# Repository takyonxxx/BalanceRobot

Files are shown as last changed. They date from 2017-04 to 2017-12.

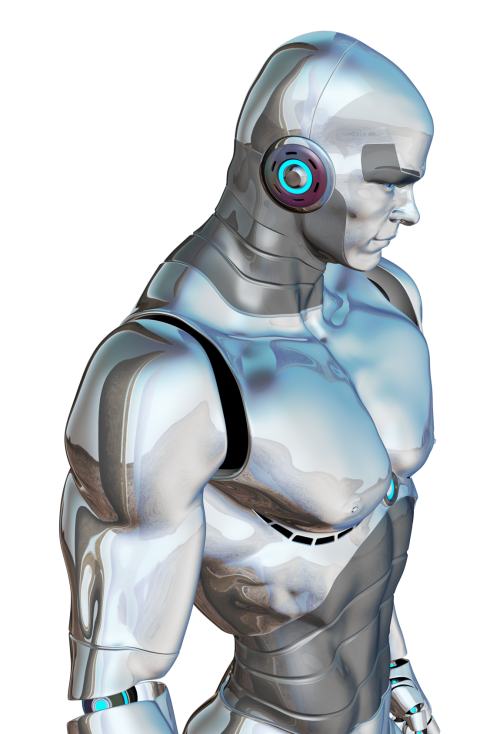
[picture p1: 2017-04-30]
Android/BalanceRobot/PNGPIX-COM-Robot-PNG-Transparent-Image-500x734.png

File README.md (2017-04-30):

Balance Robot Arduino Due or Mega

The Balance Robot uses:

18650 battery holder,

Arduino DUE / MEGA,

2 x 12V 37mm 350 Rpm 30:1 DC GearMotor with Encoder

MPU6050 (6-axis motion-tracking device that combines a 3-axis gyroscope and a 3-axis accelerometer)
With MPU6050 , you can get stable angle when the Kalman filter is used.

L298P motor driver:
is a high voltage (50V), high current (2A) dual channel full-bridge driver.
It can drive inductive loads such as relay, DC, and stepping motors.

Serial Bluetooth Module HC-06

Acrylic board

Video:
https://vimeo.com/212365258

Calibrating your PID Controller

Create some way in which you can change the PID constant of your robot while it is running.
One option is to use a potentiometer or some other analogue input to be able to increase or decrease the PID constant. 
I personally used the USB connection and the serial monitor to send new PID values.
This is important as you can then see straightaway how well the new PID values are working, and you won’t have to re-upload the code hundreds of times!
Set all PID constants to zero. This is as good a place to start as any…
Slowly increase the P-constant value.
While you are doing this, hold the robot to make sure it doesn’t fall over and smash into a million pieces!
You should increase the P-constant until the robot responds quickly to any tilting, and then just makes the robot overshoot in the other direction.
Now increase the I-constant.
This component is a bit tricky to get right.
You should keep this relatively low, as it can accumulate errors very quickly.
In theory, the robot should be able to stabilise with only the P and I constants set, but will oscillate a lot and ultimately fall over.
Raise the D-constant.
A lot. The derivative components works against any motion, so it helps to dampen any oscillations and reduce overshooting.

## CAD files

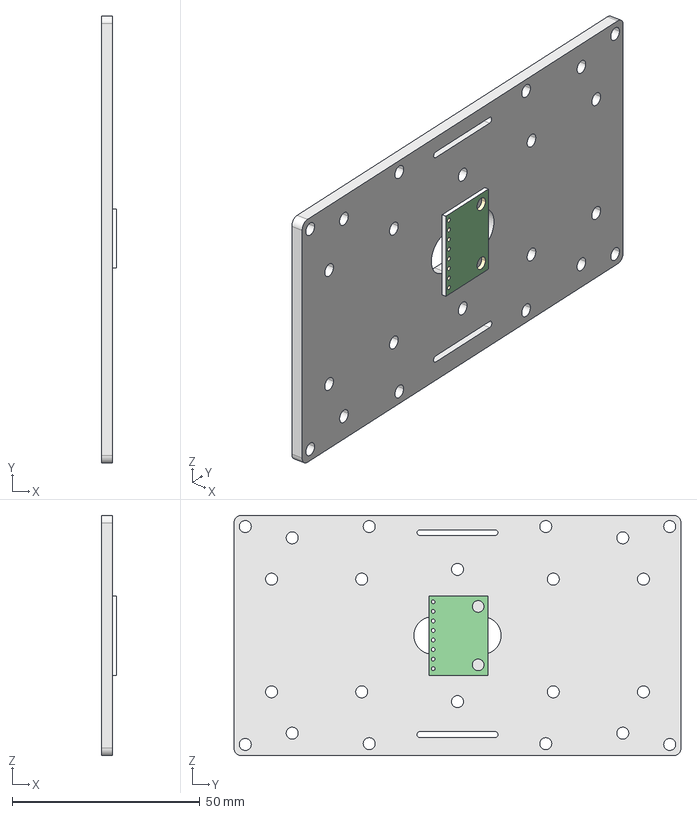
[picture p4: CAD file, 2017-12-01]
balance_mpu6050.stp
4.08 x 119.0 x 64.0 mm

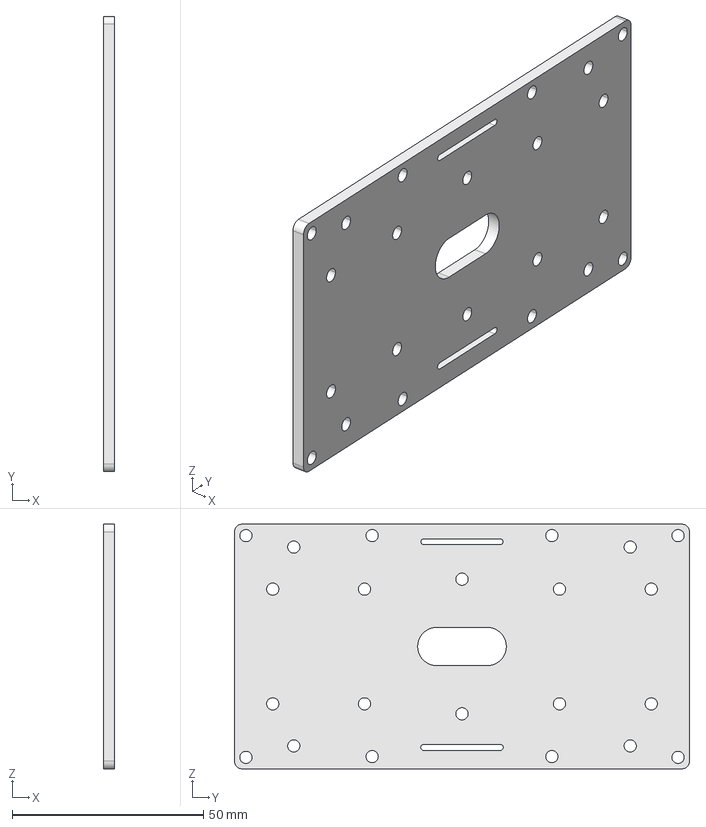
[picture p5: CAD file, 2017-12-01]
balancerobot.stp
3.00 x 119.0 x 64.0 mm

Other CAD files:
balancerobot2d.fcstd
balancerobot.stl

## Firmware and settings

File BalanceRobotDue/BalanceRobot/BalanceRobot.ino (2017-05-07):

#include <Wire.h>
#include <Kalman.h> 
#include "ComPacket.h"
#include <DueFlashStorage.h>
#include "NewPing.h"
#include "PID_v1.h"

#define RESTRICT_PITCH 
#define GUARD_GAIN 5

//motor  define L298P
#define PWM_L 2  //M1 ENA
#define PWM_R 3  //M2 ENB

#define pingPin 9 // Trigger Pin of Ultrasonic Sensor
#define echoPin 8 // Echo Pin of Ultrasonic Sensor

#define DIR_L1 5 //IN2
#define DIR_L2 4 //IN1
#define DIR_R1 7 //IN4
#define DIR_R2 6 //IN3

//encoder define
#define SPD_INT_R 13   //interrupt R
#define SPD_PUL_R 12  
#define SPD_INT_L 11   //interrupt L
#define SPD_PUL_L 10   

// Rutine for repeat part of the code every X miliseconds
#define runEvery(t) for (static long _lasttime;\
                         (uint16_t)((uint16_t)millis() - _lasttime) >= (t);\
                         _lasttime += (t))

#define MAX_DISTANCE 200 // Maximum distance we want to ping for (in centimeters). Maximum sensor distance is rated at 400-500cm.
NewPing sonar(pingPin, echoPin, MAX_DISTANCE); // NewPing setup of pins and maximum distance.

// kalman variables for sonar
float varSonar = 1.12184278324081E-05;  // variance determined using excel and reading samples of raw sensor data
float varProcess = 1e-8;
float Pc = 0.0;
float G = 0.0;
float P = 1.0;
float Xp = 0.0;
float Zp = 0.0;
float Xe = 0.0;

float distance = MAX_DISTANCE;

Kalman kalmanX; 
Kalman kalmanY;

ComPacket SerialPacket;

/* IMU Data */
double accX, accY, accZ;
double gyroX, gyroY, gyroZ;
double temperature;
int16_t tempRaw;

double gyroXangle, gyroYangle; // Angle calculate using the gyro only
double compAngleX, compAngleY; // Calculated angle using a complementary filter
double kalAngleX, kalAngleY; // Calculated angle using a Kalman filter

uint32_t timer;
uint8_t i2cData[14]; // Buffer for I2C data


int Speed_L,Speed_R;
int mSpeed,pwm_l,pwm_r;

int Speed_Need,Turn_Need;
int Speed_Diff,Speed_Diff_ALL;

double Angle_Car;
double Gyro_Car;
double Correction;

char buf[100];

uint8_t sensorPin = A0; 


//speed control values
long lastSpeedError = 0;
long speedAdjust = 0;
long dSpeedError,adjustLMotor,adjustRMotor;
long SKp ,SKi ,SKd;

int Position_AVG = 0;

float ftmp = 0;

DueFlashStorage dueFlashStorage;

struct storedData {
  float kp;
  float ki;
  float kd;
  int kc;
};

storedData m_storedData;

/////////////

#define SAMPLE_TIME 10

double Setpoint, Input, Output;

double aggKp, aggKi, aggKd;

//Specify the links and initial tuning parameters
PID balancePID(&Input, &Output, &Setpoint, aggKp, aggKi, aggKd, DIRECT);

void setup() {

  Serial.begin(115200);
  Serial1.begin(115200);

  aggKp=190;
  aggKi=425;
  aggKd=2.55;
   
  Serial.print("\nBalance Robot Initializing...\n"); 

  uint8_t codeRunningForTheFirstTime = dueFlashStorage.read(0); // flash bytes will be 255 at first run
 
  if (codeRunningForTheFirstTime) {    
    /* OK first time running, set defaults */
    m_storedData.kp = aggKp;
    m_storedData.ki = aggKi;
    m_storedData.kd = aggKd; 
    m_storedData.kc = Correction; 
    
    // write configuration struct to flash at adress 4
    byte b2[sizeof(storedData)]; // create byte array to store the struct
    memcpy(b2, &m_storedData, sizeof(storedData)); // copy the struct to the byte array
    dueFlashStorage.write(4, b2, sizeof(storedData)); // write byte array to flash

    // write 0 to address 0 to indicate that it is not the first time running anymore
    dueFlashStorage.write(0, 0); 
  }  
 
 /* read configuration struct from flash */
  byte* b = dueFlashStorage.readAddress(4); // byte array which is read from flash at adress 4
  storedData configurationFromFlash; // create a temporary struct
  memcpy(&configurationFromFlash, b, sizeof(storedData)); // copy byte array to temporary struct

  aggKp = configurationFromFlash.kp;
  aggKi = configurationFromFlash.ki;
  aggKd = configurationFromFlash.kd;
  Correction = configurationFromFlash.kc;

  Serial.print("Kp:");
  Serial.print(aggKp);

  Serial.print(" Ki:");
  Serial.print(aggKi);

  Serial.print(" Kd:");
  Serial.print(aggKd);

  Serial.print(" Correction:");
  Serial.print(Correction);

  Init();

  initGyro();  

  Setpoint = 0;  

    //setup PID    
  balancePID.SetMode(AUTOMATIC);
  balancePID.SetSampleTime(SAMPLE_TIME);
  balancePID.SetOutputLimits(-255, 255);  
  
  timer = micros();   
}

void Init()
{  
  
  pinMode(SPD_PUL_L, INPUT);
  pinMode(SPD_PUL_R, INPUT);
  pinMode(SPD_INT_L, INPUT_PULLUP);
  pinMode(SPD_INT_R, INPUT_PULLUP);
  
  pinMode(PWM_L, OUTPUT);
  pinMode(PWM_R, OUTPUT);
  pinMode(DIR_L1, OUTPUT);
  pinMode(DIR_L2, OUTPUT);
  pinMode(DIR_R1, OUTPUT);
  pinMode(DIR_R2, OUTPUT); 

  pinMode(pingPin, OUTPUT);
  pinMode(echoPin, INPUT);
  
  //init variables
  Speed_L = 0;
  Speed_R = 0;
 
  mSpeed = 0; pwm_l = 0; pwm_r = 0;
  Speed_Diff = 0;Speed_Diff_ALL = 0;   
  
  Speed_Need = 0;
  Turn_Need = 0;
  Correction = 0;

  //motor speed difference (Left-Right) correction
  lastSpeedError = 0;
  speedAdjust = 0;
  dSpeedError = 0;
  adjustLMotor = 0;
  adjustRMotor = 0;
  SKp = 1L;
  SKi = 0.5L;
  SKd = 0.3L;  

  attachInterrupt(SPD_INT_L, Encoder_L,FALLING);
  attachInterrupt(SPD_INT_R, Encoder_R,FALLING);   
 
  //lastTime = millis() - SampleTime;
  
}

double getVoltage(uint8_t sensorPin,uint16_t refVoltage,float dividerRatio) {    
  analogReadResolution(12);  //A0 
  double reading = analogRead(sensorPin) * dividerRatio * refVoltage / 4096 / 1000;   
  delay(2); // allow the ADC to stabilize
  return reading;
}

float getFilteredSonar()
{  
  long sonar_value = sonar.ping_cm();
  
   // kalman process
  Pc = P + varProcess;
  G = Pc/(Pc + varSonar);    // kalman gain
  P = (1-G)*Pc;
  Xp = Xe;
  Zp = Xp;
  Xe = G*(sonar_value-Zp)+Xp;   // the kalman estimate of the sensor voltage

  return Xe;
}

void MySerialEvent()
{
  uchar c = '0';
  uchar tmp = 0;
  
  if(Serial1.available()) {
    
    c = (uchar)Serial1.read(); 
   
    for(int i = 5; i > 0; i--)
    {
       SerialPacket.m_Buffer[i] = SerialPacket.m_Buffer[i-1];
    }
    
    SerialPacket.m_Buffer[0] = c;
    
    if(SerialPacket.m_Buffer[5] == 0xAA)
    {
       tmp = SerialPacket.m_Buffer[1]^SerialPacket.m_Buffer[2]^SerialPacket.m_Buffer[3];
       if(tmp == SerialPacket.m_Buffer[0])
       {
         SerialPacket.m_PackageOK = true;         
       }
    } 
  } 
}

void UserComunication()
{
  MySerialEvent();  
  
  if(SerialPacket.m_PackageOK == true)
  {    
    SerialPacket.m_PackageOK = false;     
   
    switch(SerialPacket.m_Buffer[4])
    {      
      case 0x01:  break;
      case 0x02: UpdatePID();break;
      case 0x03: CarDirection();break;
      case 0x04:  break;
      case 0x05:  break;                  
      case 0x06:  break;
      case 0x07:  break;
      default:    break;             
    }
  }  
}

void CarDirection()
{    
  unsigned char Speed = SerialPacket.m_Buffer[1];
  switch(SerialPacket.m_Buffer[3])
  {
    case 0x00: Speed_Need = 0;Turn_Need = 0;break;
    case 0x01: Speed_Need = -Speed; break;
    case 0x02: Speed_Need = Speed; break;
    case 0x03: Turn_Need = Speed; break;
    case 0x04: Turn_Need = -Speed; break;
    case 0x05: Correction = Correction + 0.1;UpdateCorrection(); break;
    case 0x06: Correction = Correction - 0.1;UpdateCorrection(); break;
    default:break;
  }     
}

void UpdateCorrection()
{
  m_storedData.kc = Correction; 

  // write configuration struct to flash at adress 4
  byte b2[sizeof(storedData)]; // create byte array to store the struct
  memcpy(b2, &m_storedData, sizeof(storedData)); // copy the struct to the byte array
  dueFlashStorage.write(4, b2, sizeof(storedData)); // write byte array to flash

  // write 0 to address 0 to indicate that it is not the first time running anymore
  dueFlashStorage.write(0, 0); 
}

void loop() {      
unsigned long timeSerial = millis();  

    while(1)
    { 
      if(calculateGyro())
      {  
          PWM_Calculate();
          Car_Control();    
          //distance = getFilteredSonar();   
           
          sprintf(buf, "Data:%d:%d:%0.1f:%d:%d:%d:%d:%0.2f:%0.2f:%0.2f:%0.1f:%d:%0.1f>", 
          pwm_l, pwm_r,Angle_Car,Speed_Need,Turn_Need,Speed_L,Speed_R,aggKp,aggKi,aggKd,temperature,Position_AVG,Correction);           
          Serial1.println(buf);    
          
          /*sprintf(buf, "pwm_l:%d  pwm_r:%d  Position_Add:%d  Angle_Car:%0.1f  Gyro_Car:%0.1f Speed_Need:%d",pwm_l,pwm_r,Position_AVG,Angle_Car,Gyro_Car,Speed_Need);     
          Serial.println(buf);*/
      }  

      UserComunication();         
      
    }    
}

void initGyro() { 
  
  Wire.begin();
  #if ARDUINO >= 157
    Wire.setClock(400000UL); // Set I2C frequency to 400kHz
  #else
    TWBR = ((F_CPU / 400000UL) - 16) / 2; // Set I2C frequency to 400kHz
  #endif

  i2cData[0] = 7; // Set the sample rate to 1000Hz - 8kHz/(7+1) = 1000Hz
  i2cData[1] = 0x00; // Disable FSYNC and set 260 Hz Acc filtering, 256 Hz Gyro filtering, 8 KHz sampling
  i2cData[2] = 0x00; // Set Gyro Full Scale Range to ±250deg/s
  i2cData[3] = 0x00; // Set Accelerometer Full Scale Range to ±2g
  while (i2cWrite(0x19, i2cData, 4, false)); // Write to all four registers at once
  while (i2cWrite(0x6B, 0x01, true)); // PLL with X axis gyroscope reference and disable sleep mode

  while (i2cRead(0x75, i2cData, 1));
  if (i2cData[0] != 0x68) { // Read "WHO_AM_I" register
    Serial.print(F("Error reading sensor"));
    while (1);
  }

  delay(100); // Wait for sensor to stabilize

  /* Set kalman and gyro starting angle */
  while (i2cRead(0x3B, i2cData, 6));
  accX = (int16_t)((i2cData[0] << 8) | i2cData[1]);
  accY = (int16_t)((i2cData[2] << 8) | i2cData[3]);
  accZ = (int16_t)((i2cData[4] << 8) | i2cData[5]);

#ifdef RESTRICT_PITCH // Eq. 25 and 26
  double roll  = atan2(accY, accZ) * RAD_TO_DEG;
  double pitch = atan(-accX / sqrt(accY * accY + accZ * accZ)) * RAD_TO_DEG;
#else // Eq. 28 and 29
  double roll  = atan(accY / sqrt(accX * accX + accZ * accZ)) * RAD_TO_DEG;
  double pitch = atan2(-accX, accZ) * RAD_TO_DEG;
#endif

  kalmanX.setAngle(roll); // Set starting angle
  kalmanY.setAngle(pitch);

  gyroXangle = roll;
  gyroYangle = pitch;
  compAngleX = roll;
  compAngleY = pitch;  

}

int calculateGyro()
{ 
  if((micros() - timer) >= 10000) 
  {    //10ms 
     /* Update all the values */
    while (i2cRead(0x3B, i2cData, 14));
    accX = (int16_t)((i2cData[0] << 8) | i2cData[1]);
    accY = (int16_t)((i2cData[2] << 8) | i2cData[3]);
    accZ = (int16_t)((i2cData[4] << 8) | i2cData[5]);
    tempRaw = (int16_t)((i2cData[6] << 8) | i2cData[7]);
    gyroX = (int16_t)((i2cData[8] << 8) | i2cData[9]);
    gyroY = (int16_t)((i2cData[10] << 8) | i2cData[11]);
    gyroZ = (int16_t)((i2cData[12] << 8) | i2cData[13]);;
    
    double dt = (double)(micros() - timer) / 1000000; // Calculate delta time
    timer = micros();
    
    // It is then converted from radians to degrees
    #ifdef RESTRICT_PITCH // Eq. 25 and 26
    double roll  = atan2(accY, accZ) * RAD_TO_DEG;
    double pitch = atan(-accX / sqrt(accY * accY + accZ * accZ)) * RAD_TO_DEG;
    #else // Eq. 28 and 29
    double roll  = atan(accY / sqrt(accX * accX + accZ * accZ)) * RAD_TO_DEG;
    double pitch = atan2(-accX, accZ) * RAD_TO_DEG;
    #endif
    
    double gyroXrate = gyroX / 131.0; // Convert to deg/s
    double gyroYrate = gyroY / 131.0; // Convert to deg/s
    
    #ifdef RESTRICT_PITCH
    // This fixes the transition problem when the accelerometer angle jumps between -180 and 180 degrees
    if ((roll < -90 && kalAngleX > 90) || (roll > 90 && kalAngleX < -90)) {
      kalmanX.setAngle(roll);
      compAngleX = roll;
      kalAngleX = roll;
      gyroXangle = roll;
    } else
      kalAngleX = kalmanX.getAngle(roll, gyroXrate, dt); // Calculate the angle using a Kalman filter
    
    if (abs(kalAngleX) > 90)
      gyroYrate = -gyroYrate; // Invert rate, so it fits the restriced accelerometer reading
    kalAngleY = kalmanY.getAngle(pitch, gyroYrate, dt);
    #else
    // This fixes the transition problem when the accelerometer angle jumps between -180 and 180 degrees
    if ((pitch < -90 && kalAngleY > 90) || (pitch > 90 && kalAngleY < -90)) {
      kalmanY.setAngle(pitch);
      compAngleY = pitch;
      kalAngleY = pitch;
      gyroYangle = pitch;
    } else
      kalAngleY = kalmanY.getAngle(pitch, gyroYrate, dt); // Calculate the angle using a Kalman filter
    
    if (abs(kalAngleY) > 90)
      gyroXrate = -gyroXrate; // Invert rate, so it fits the restriced accelerometer reading
      kalAngleX = kalmanX.getAngle(roll, gyroXrate, dt); // Calculate the angle using a Kalman filter
    #endif 
    
    if (gyroXangle < -180 || gyroXangle > 180)
      gyroXangle = kalAngleX;
    if (gyroYangle < -180 || gyroYangle > 180)
      gyroYangle = kalAngleY;
    
    Angle_Car = kalAngleX;   //negative backward  positive forward
    Gyro_Car = gyroXrate;    
    
    temperature = (double)tempRaw / 340.0 + 36.53;
   
    return 1;
   }
  return 0;
}

void Encoder_L()   //car up is positive car down  is negative
{
  if (digitalRead(SPD_PUL_L))
    Speed_L += 1;
  else
    Speed_L -= 1;

  /*sprintf(buf, "Speed_L:%d  Speed_R:%d  Speed_Diff_ALL:%d",Speed_L,Speed_R,Speed_Diff_ALL);     
  Serial.println(buf);  */
                        
}

void Encoder_R()    //car up is positive car down  is negative
{
  if (!digitalRead(SPD_PUL_R))
    Speed_R += 1;
  else
    Speed_R -= 1;   

  /*sprintf(buf, "Speed_L:%d  Speed_R:%d  Speed_Diff_ALL:%d",Speed_L,Speed_R,Speed_Diff_ALL);   
  Serial.println(buf);*/
}

void correctSpeedDiff() 
{
  dSpeedError = Speed_Diff - lastSpeedError;
  
  speedAdjust = (SKp*Speed_Diff)
              + (SKi*Speed_Diff_ALL)
              + (SKd*dSpeedError);

  adjustLMotor -= speedAdjust/2 ;
  adjustRMotor += speedAdjust/2 ;  
  
  lastSpeedError = Speed_Diff;

}

bool StopFlag = true;

float integrated_error = 0;
int count = 0,last_count;
float pTerm,iTerm,dTerm,last_error,pTerm_Wheel,dTerm_Wheel;
float Kp_Wheel,Kd_Wheel,K;

int getPid(float targetPosition, float currentPosition)   {
  Kp_Wheel = 1;
  Kd_Wheel = 1;
  K=1;
  
  float error = targetPosition - currentPosition; 
  pTerm = aggKp * error;
  integrated_error += error;                                       
  iTerm = aggKi * constrain(integrated_error, -GUARD_GAIN, GUARD_GAIN);
  dTerm = aggKd * (error - last_error);                            
  last_error = error;
  
  count = -Speed_R;
  pTerm_Wheel = Kp_Wheel * count;
  dTerm_Wheel = Kd_Wheel * (count - last_count);                            
  last_count = count;
  return -K*(pTerm + iTerm + dTerm + pTerm_Wheel + dTerm_Wheel);
}


void PWM_Calculate()
{     
  Speed_Diff = Speed_L - Speed_R;
  Speed_Diff_ALL += Speed_Diff;    
 
  //correctSpeedDiff();

  ftmp = (Speed_L + Speed_R) * 0.5;
  
  if( ftmp > 0)
    Position_AVG = ftmp +0.5;  
  else
    Position_AVG = ftmp -0.5;    

  Input = Angle_Car;

  Setpoint = Correction;

  balancePID.Setpoint(&Setpoint);
  
  double gap = abs(Setpoint-Input); //distance away from setpoint
  if (gap < 10)
  {  //we're close to setpoint, use conservative tuning parameters
    balancePID.SetTunings(aggKp/3, aggKi/3, aggKd/3);
  }
  else
  {     //we're far from setpoint, use aggressive tuning parameters
     balancePID.SetTunings(aggKp, aggKi, aggKd);
  }

  balancePID.Compute(2.5 * Speed_Need);
  
  mSpeed = -constrain(Output,-255,255);    
    
  if((Speed_Need != 0) && (Turn_Need == 0))
  {
    if(StopFlag == true)
    {
      Speed_Diff_ALL = 0;
      StopFlag = false;
    }
    pwm_r = constrain(int(mSpeed - Turn_Need - adjustRMotor - Speed_Diff_ALL),-255,255);
    pwm_l = constrain(int(mSpeed + Turn_Need + adjustLMotor + Speed_Diff_ALL ),-255,255);
  
  }
  else
  {
    StopFlag = true;
    pwm_r = constrain(int(mSpeed - Turn_Need - adjustRMotor),-255,255);
    pwm_l = constrain(int(mSpeed + Turn_Need + adjustLMotor),-255,255);
  }
  
  Speed_L = 0;
  Speed_R = 0;
}

void Car_Control()
{  
 if (pwm_l>0)
  {
    digitalWrite(DIR_L1, LOW);
    digitalWrite(DIR_L2, HIGH);
  }
  if (pwm_l<0)
  {
    digitalWrite(DIR_L1, HIGH);
    digitalWrite(DIR_L2, LOW);
    pwm_l =- pwm_l;  //cchange to positive
  }
  
  if (pwm_r>0)
  {
    digitalWrite(DIR_R1, HIGH);
    digitalWrite(DIR_R2, LOW);
  }
  if (pwm_r<0)
  {
    digitalWrite(DIR_R1, LOW);
    digitalWrite(DIR_R2, HIGH);
    pwm_r = -pwm_r;
  }  
  
  if( Angle_Car > 40 || Angle_Car < -40 )
  {
    pwm_l = 0;
    pwm_r = 0;
  }

  analogWrite(PWM_L, pwm_l);
  analogWrite(PWM_R, pwm_r);    
}
void UpdatePID()
{  
  unsigned int Upper,Lower;
  double NewPara;
  Upper = SerialPacket.m_Buffer[2];
  Lower = SerialPacket.m_Buffer[1];
  NewPara = (float)(Upper<<8 | Lower)/100.0;  
  
  switch(SerialPacket.m_Buffer[3])
  {
    case 0x01:aggKp = NewPara;break; 
    case 0x02:aggKi = NewPara;break;
    case 0x03:aggKd = NewPara;break;
    default:break;
  }

  sprintf(buf,"UpdatePID: %0.2X VAL: %0.2f Kp: %0.2f Ki: %0.2f Kd: %0.2f",SerialPacket.m_Buffer[3],NewPara,aggKp,aggKi,aggKd);
  Serial.println(buf); 
 
  m_storedData.kp = aggKp;
  m_storedData.ki = aggKi;
  m_storedData.kd = aggKd; 

  // write configuration struct to flash at adress 4
  byte b2[sizeof(storedData)]; // create byte array to store the struct
  memcpy(b2, &m_storedData, sizeof(storedData)); // copy the struct to the byte array
  dueFlashStorage.write(4, b2, sizeof(storedData)); // write byte array to flash

  // write 0 to address 0 to indicate that it is not the first time running anymore
  dueFlashStorage.write(0, 0); 
}

/*// PID-control values
float pTerm = 0;
float iTerm = 0; // Used to accumalate error (intergral)
float dTerm = 0;

float Kp;// (P)roportional Tuning Parameter
float Ki;// (I)ntegral Tuning Parameter        
float Kd;// (D)erivative Tuning Parameter 

float lastError = 0;                // Keeps track of error over time
float targetAngle = 0;          // Can be adjusted according to centre of gravity            

double lastTime = 0;
double SampleTime = 10;


int setPidPwm(float pitch)   {  
 
  float error = targetAngle - pitch;
  
  pTerm = Kp * error + Correction;                                              
  iTerm = Ki * abs(Gyro_Car) - 2 * Speed_Need;
  dTerm = Kd * (error - lastError) * constrain(Position_Add/25, - GUARD_GAIN, GUARD_GAIN);                       
  lastError = error;  
 
  float PIDValue = -constrain((pTerm + iTerm + dTerm), -255, 255);   
  return int(PIDValue);
}*/

/*
Proportional – present error
The present error is the amount of tilt that the robot has. 
It is supposed to have a tilt of 0°. If it is tiled by 10°, the error is -10.

Integral – sum of accumulated errors
The sum of errors accumulated. For the self balancing robot, this value is zero.

Derivative – expected future error
The error we expect to have on the next iteration of this algorithm.
The current tilt may be 10°, and we may be expecting it to become 11° on the next iteration.
The algorithm takes this into account when it decides how much force to apply on the wheels.

Calibrating your PID Controller

Create some way in which you can change the PID constant of your robot while it is running.
One option is to use a potentiometer or some other analogue input to be able to increase or decrease the PID constant. 
I personally used the USB connection and the serial monitor to send new PID values.
This is important as you can then see straightaway how well the new PID values are working, and you won’t have to re-upload the code hundreds of times!
Set all PID constants to zero. This is as good a place to start as any…
Slowly increase the P-constant value.
While you are doing this, hold the robot to make sure it doesn’t fall over and smash into a million pieces!
You should increase the P-constant until the robot responds quickly to any tilting, and then just makes the robot overshoot in the other direction.
Now increase the I-constant.
This component is a bit tricky to get right.
You should keep this relatively low, as it can accumulate errors very quickly.
In theory, the robot should be able to stabilise with only the P and I constants set, but will oscillate a lot and ultimately fall over.
Raise the D-constant.
A lot. The derivative components works against any motion, so it helps to dampen any oscillations and reduce overshooting.
I found that this constant has to be set significantly higher than the other two (x10 to x100 more) in order to have any effect.
All the same, don’t set it too high, as it will reduce the robot’s ability to react to external forces (aka. being pushed around).
Spend many fruitless hours slightly modifying the PID values.
This is probably the longest part of the procedure, as there isn’t much of a method to it. 
You just have to increase and decrease the values until you reach that perfect sweet-spot for your robot!

What P, I & D values means practically?
In case of Self-Balancing Robot-

P-P determines the force with which the robot will correct itself. A lower P shows robot’s inability to balance itself and a higher P will shows the violent behavior.
I-I determines the response time of robot for correcting itself. Higher the P, Faster it will response.
D- D determines the sensitivity of robot to the error in its state. It is used to smoothen/depress the robot oscillations. A lower D is unable to remove oscillations and a higher D will cause violent vibrations.*/

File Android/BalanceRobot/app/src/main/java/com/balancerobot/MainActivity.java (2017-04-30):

package com.balancerobot;

import android.app.Activity;
import android.app.AlertDialog;
import android.bluetooth.BluetoothAdapter;
import android.bluetooth.BluetoothDevice;
import android.content.Context;
import android.content.DialogInterface;
import android.content.Intent;
import android.content.SharedPreferences;
import android.content.res.Configuration;
import android.graphics.Color;
import android.hardware.Sensor;
import android.hardware.SensorEvent;
import android.hardware.SensorEventListener;
import android.hardware.SensorManager;
import android.os.Bundle;
import android.os.Handler;
import android.os.Message;
import android.os.PowerManager;
import android.preference.PreferenceManager;

import android.support.v7.app.ActionBarActivity;
import android.support.v7.widget.Toolbar;
import android.view.KeyEvent;
import android.view.LayoutInflater;
import android.view.Menu;
import android.view.MenuItem;
import android.view.MotionEvent;
import android.view.View;
import android.view.ViewGroup;
import android.view.WindowManager;
import android.view.inputmethod.EditorInfo;
import android.widget.ArrayAdapter;
import android.widget.Button;
import android.widget.EditText;
import android.widget.ListView;
import android.widget.SeekBar;
import android.widget.TextView;
import android.widget.Toast;

import java.util.InputMismatchException;
import java.util.StringTokenizer;

public class MainActivity extends ActionBarActivity {

    private static final String TAG = "MainActivity";

    private Context mContext;
    private static MainActivity mContext1;
    private View menuView;


    MenuItem itemtemp;
    byte[] commandPacket = new byte[11];
    byte[] commandPacket1 = new byte[2];
    byte[] commandPacket2 = new byte[4];
    static byte[] commandPacketBlueTooth = new byte[6];

    public static int Kp = 0;
    public static int Ki = 0;
    public static int Kd = 0;

    private Button Pids;
    private Button Forward;
    private Button Back;
    private Button Left;
    private Button Right;
    private Button Stop;
    private Button C_Plus;
    private Button C_Mines;

    static TextView textView_Speed1;
    static TextView textView_Speed2;
    static TextView  textPwmL;
    static TextView  textPwmR;
    static TextView  textSpeedL;
    static TextView  textAngle;
    static TextView  textSpeedR;

    static SeekBar seekBar_Speed1;
    static SeekBar seekBar_Speed2;

    private int speed1;
    private int speed2;

    private int azimuth;
    private int pitch;
    private int roll;
    private SensorManager mSensorManager;

    public static final int MESSAGE_STATE_CHANGE = 1;
    public static final int MESSAGE_READ = 2;
    public static final int MESSAGE_WRITE = 3;
    public static final int MESSAGE_DEVICE_NAME = 4;
    public static final int MESSAGE_TOAST = 5;
    // Key names received from the BluetoothChatService Handler
    public static final String DEVICE_NAME = "device_name";
    public static final String TOAST = "toast";
    // Intent request codes
    private static final int REQUEST_CONNECT_DEVICE = 2;
    private static final int REQUEST_ENABLE_BT = 3;

    BluetoothDevice currentdevice;
    boolean commandmode = false, initialized = false, tryconnect = false;
    Intent serverIntent = null;

    private PowerManager.WakeLock wl;
    private Menu menu;
    private EditText mOutEditText;
    private TextView statusText;
    private Button mSendButton;
    private ListView mConversationView;
    private String mConnectedDeviceName = "Ecu";
    // Local Bluetooth adapter
    private BluetoothAdapter mBluetoothAdapter = null;
    // Member object for the chat services
    private static BluetoothService  mBtService = null;

    // The Handler that gets information back from the BluetoothChatService
    // Array adapter for the conversation thread
    private ArrayAdapter<String> mConversationArrayAdapter;

    private final Handler mBtHandler = new Handler() {
        @Override
        public void handleMessage(Message msg) {

            switch (msg.what) {
                case MESSAGE_STATE_CHANGE:

                    switch (msg.arg1) {
                        case BluetoothService.STATE_CONNECTED:
                            statusText.setText(getString(R.string.title_connected_to, mConnectedDeviceName));
                            try {
                                itemtemp = menu.findItem(R.id.menu_connect_bt);
                                itemtemp.setTitle(R.string.disconnectbt);
                            } catch (Exception e) {
                            }
                            break;
                        case BluetoothService.STATE_CONNECTING:
                            statusText.setText(R.string.title_connecting);
                            break;
                        case BluetoothService.STATE_LISTEN:

                        case BluetoothService.STATE_NONE:
                            statusText.setText(R.string.title_not_connected);
                            itemtemp = menu.findItem(R.id.menu_connect_bt);
                            itemtemp.setTitle(R.string.connectbt);
                            break;
                    }
                    break;
                case MESSAGE_WRITE:

                    byte[] writeBuf = (byte[]) msg.obj;
                    String writeMessage = new String(writeBuf);

                    if (commandmode || !initialized) {
                        mConversationArrayAdapter.add("Command:  " + writeMessage);
                    }

                    break;
                case MESSAGE_READ:

                    String tmpmsg = clearMsg(msg);

                    if(tmpmsg.contains("Data:"))
                    {
                        String Title = "Data";
                        String Pwml = "0";
                        String Pwmr = "0";
                        String Angle ="0";
                        String Speed_Need = "0";
                        String Turn_Need = "0";
                        String Speed_L = "0";
                        String Speed_R = "0";
                        String Temperature = "0";
                        String KP = "0";
                        String KI = "0";
                        String KD = "0";
                        String Ultarsonic_Distance = "0";
                        String Position_Add = "0";
                        String Correction = "0";

                        StringTokenizer token = new StringTokenizer(tmpmsg, ":");

                        if(token.hasMoreTokens()) {
                             Title = token.nextToken();
                        }
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

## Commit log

2017-12-01 Freecad drawings
    [balancerobot.stl, balancerobot.stp, balancerobot2d.fcstd]
2017-12-01 Freecad Files
    [balance_mpu6050.stp]
